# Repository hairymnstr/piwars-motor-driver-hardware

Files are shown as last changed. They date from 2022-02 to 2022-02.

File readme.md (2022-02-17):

# Motor and Servo Driver Board

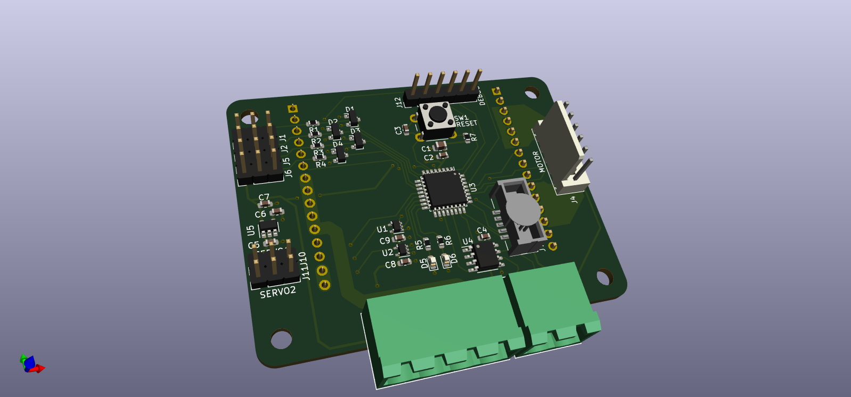
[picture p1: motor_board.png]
Motor and Servo control board


This small board was designed for our robot in PiWars 2021.
It's designed to drive a small DC motor up to ~4A/12V with optional quadrature encoder feedback and up to two servo motors.
The board interfaces with a host system via RS485 and its address is set with three jumpers on the board, so you can have up to 8 of these on a single 485 bus.
In the competition we used 6 of these, four for our all-wheel steering robot and two for a grab arm.  In total we used 6 servos and 6 DC motors.  All were controlled via a RaspberryPi with negligible lag.

The actual H-bridge in this module is an ST VNH7070AS mounted on an eval board. <https://uk.farnell.com/stmicroelectronics/ev-vnh7070as/eval-board-high-bridge-motor-driver>  I chose the eval board option because the part had a thermal slug underneath it and I didn't have a way to surface mount it at home.

## Issues

There are a couple of issues with the current board:

1. The servo connector pinout is wrong for all standard servos.  When I designed the board I didn't think to check and placed the signal in the middle pin between the power and ground.  RC servos are normally Gnd-Pwr-Sig.  You can work around this by carefully removing the signal and power wires from the connector shell and re-inserting them in the special order required.

2. There should be a bulk capacitor on the 5V rail.  Our robot had a big (3A) 5V regulator which powered all the control electronics so these boards were designed to use that as the power for their logic (via a 3.3V low input regulator) and the servos.  Using MG996R servos I kept "popping" the 3.3V regulator.  The fix was to add a bulk capacitance locally to smooth out the spikes caused by the servo.  In my current design I'm also coupling each board with an LM2596 DC-DC regulator to generate 6V for the servos and feed the 3.3V regulator so the whole assembly only needs a wide-range raw battery voltage input.

## Firmware

Firmware is in another repository and currently only supports one motor without encoder and a single servo.  See <https://github.com/hairymnstr/piwars-motor-driver-firmware>.

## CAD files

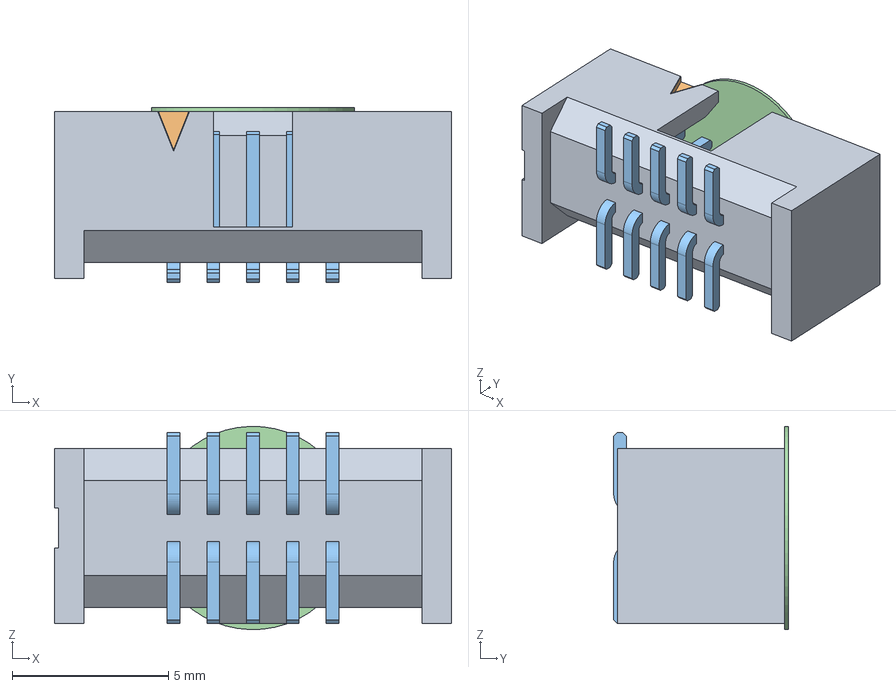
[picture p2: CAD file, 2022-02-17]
SHF-105-01-L-D-SM-K-TR.stp
12.7 x 5.59 x 6.50 mm
_SHF-105-01-D_header
_SHF-First_Position_Indicator
_T-1S71-02-05-D-SM
_K-DOT-0.256-0.375-0.005_polyamide_pick_

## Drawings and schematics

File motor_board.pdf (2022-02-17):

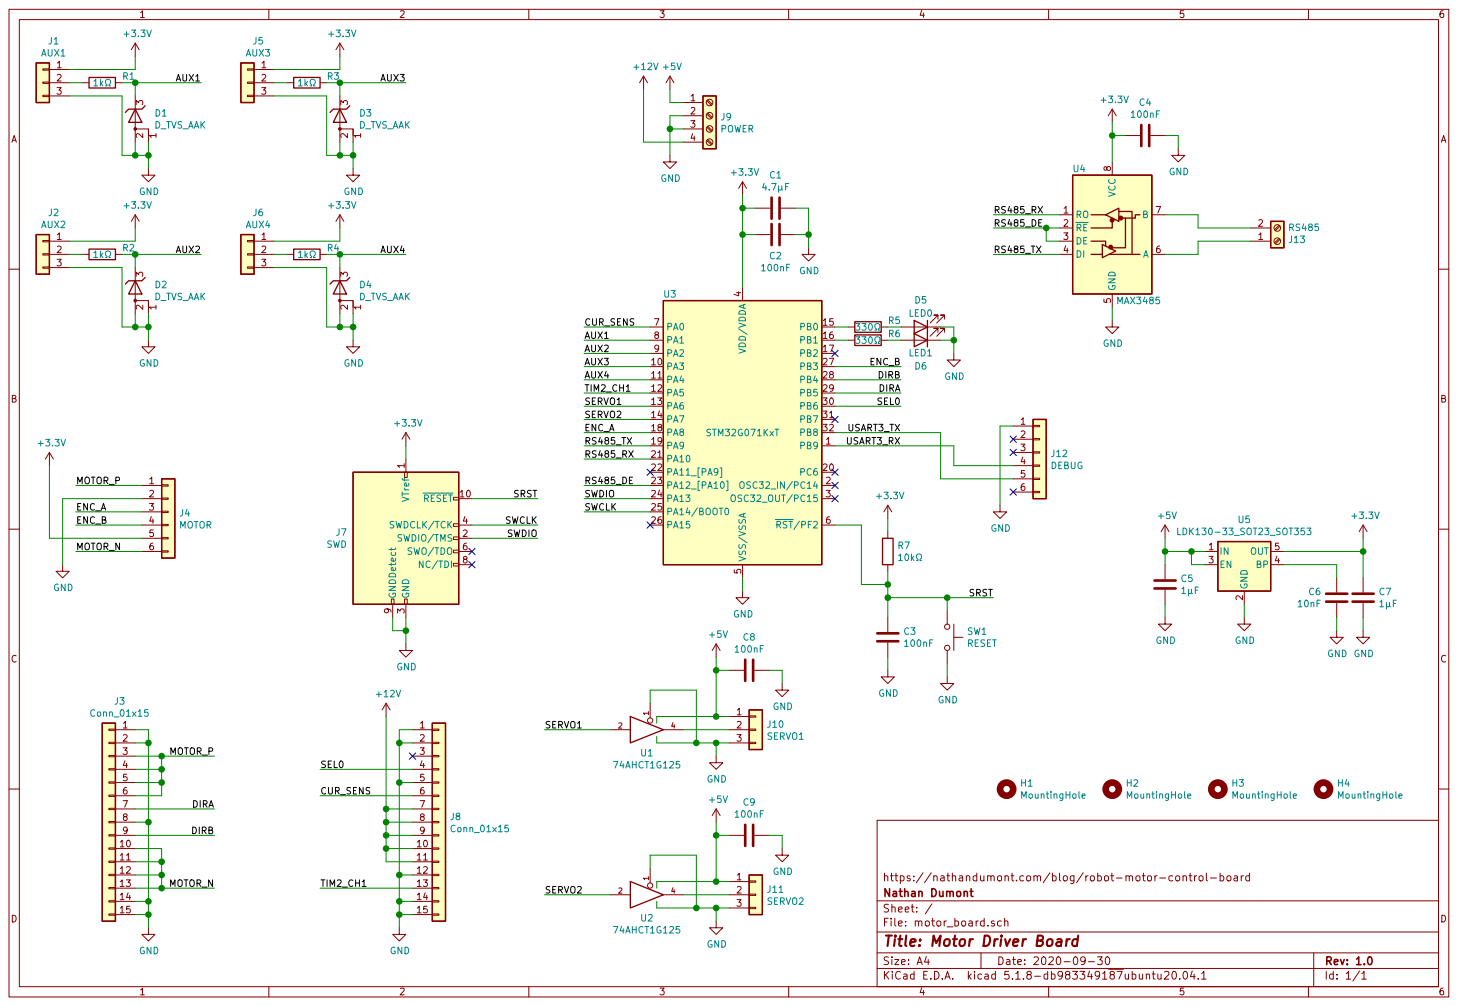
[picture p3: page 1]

3 SWDCLK/TCK 4 SWO/TDO 6 NC/TDI 8 GNDDetect 9

File: motor_board.sch Sheet: / Nathan Dumont https://nathandumont.com/blog/robot-motor-control-board

Id: 1/1 Title: Motor Driver Board

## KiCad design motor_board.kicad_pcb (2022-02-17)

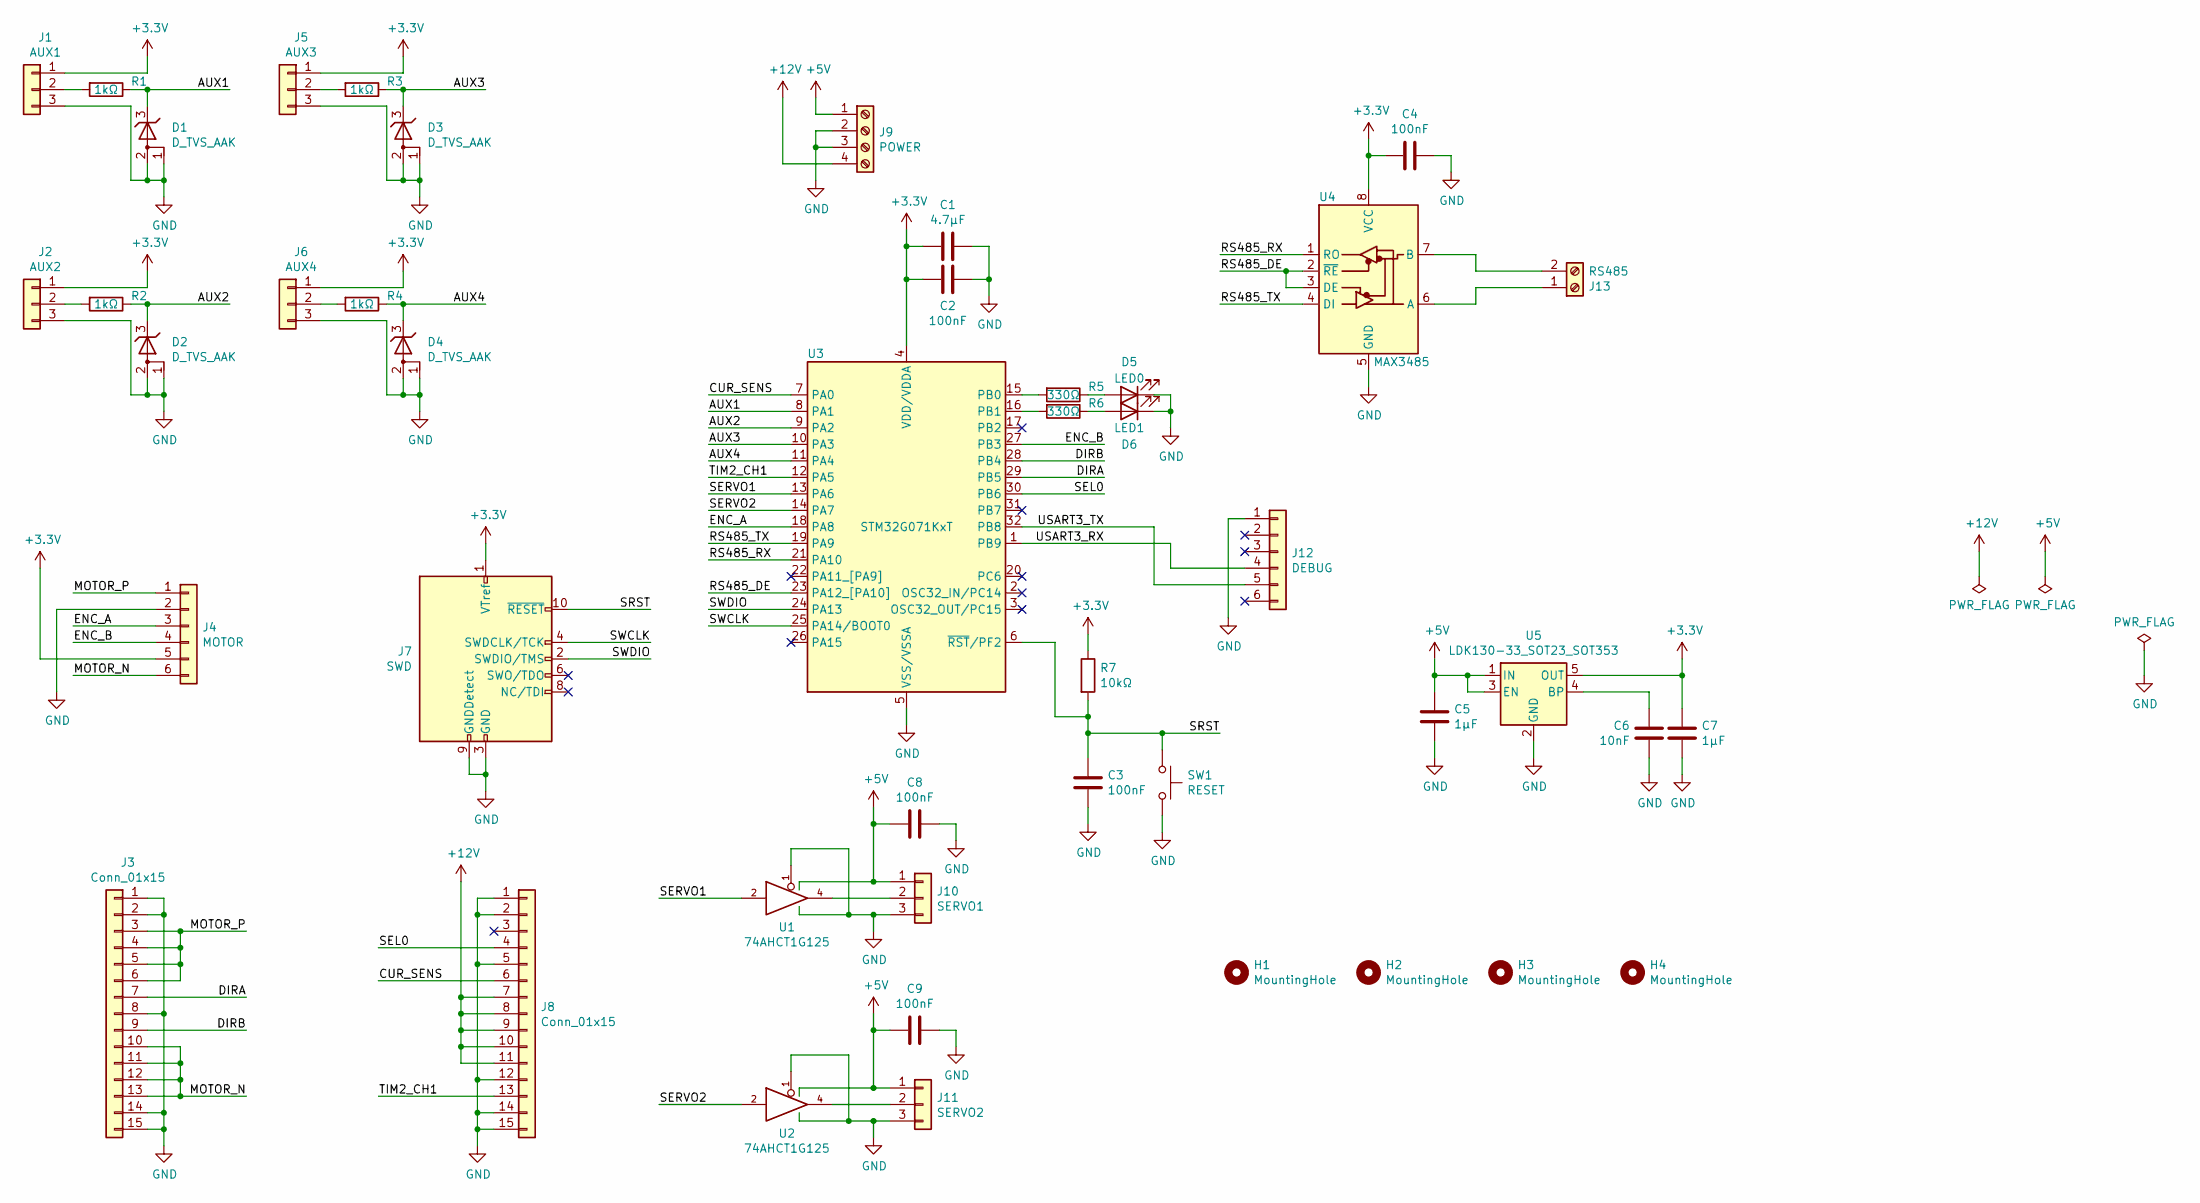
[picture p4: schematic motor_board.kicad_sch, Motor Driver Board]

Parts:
C1: 4.7µF; C_0805_2012Metric
C2, C3, C4, C8, C9: 100nF; C_0603_1608Metric
C5, C7: 1µF; C_0603_1608Metric
C6: 10nF; C_0603_1608Metric
D1, D2, D3, D4: D_TVS_AAK; SOT-23; Part number BOURNS CDSOT23-T03-Q; Farnell 3015164
D5: LED0; LED_0603_1608Metric; Part number KINGBRIGHT KPT-1608EC; Farnell 2099221
D6: LED1; LED_0603_1608Metric; Part number KINGBRIGHT KPH-1608SGC; Farnell 2426215
H1, H2, H3, H4: MountingHole; MountingHole_3.2mm_M3
J1: AUX1; PinHeader_1x03_P2.54mm_Vertical
J2: AUX2; PinHeader_1x03_P2.54mm_Vertical
J3: Conn_01x15; PinHeader_1x15_P2.54mm_Vertical
J4: MOTOR; Molex_KK-254_AE-6410-06A_1x06_P2.54mm_Vertical; Part number MOLEX 22-27-2061; Farnell 9731172
J5: AUX3; PinHeader_1x03_P2.54mm_Vertical
J6: AUX4; PinHeader_1x03_P2.54mm_Vertical
J7: SWD; SAMTEC_SHF-SM_5x2
J8: Conn_01x15; PinSocket_1x15_P2.54mm_Vertical
J9: POWER; PhoenixContact_MSTBA_2,5_4-G-5,08_1x04_P5.08mm_Horizontal; Part number PHOENIX CONTACT MSTBA 2,5/ 4-G-5,08; Farnell 3705195
J10: SERVO1; PinHeader_1x03_P2.54mm_Vertical
J11: SERVO2; PinHeader_1x03_P2.54mm_Vertical
J12: DEBUG; PinHeader_1x06_P2.54mm_Vertical
J13: RS485; PhoenixContact_MSTBA_2,5_2-G-5,08_1x02_P5.08mm_Horizontal; Part number PHOENIX CONTACT MSTBA 2,5/ 2-G-5,08; Farnell 3705171
R1, R2, R3, R4: 1kΩ; R_0603_1608Metric
R5, R6: 330Ω; R_0603_1608Metric; Part number MULTICOMP MCWR06X3300FTL; Farnell 2447339
R7: 10kΩ; R_0603_1608Metric
SW1: RESET; SW_PUSH_6mm
U1, U2: 74AHCT1G125; SOT-353_SC-70-5; Part number TI SN74AHCT1G125DCKR; Farnell 3006131
U3: STM32G071KxT; LQFP-32_7x7mm_P0.8mm; Part number ST STM32G071KBT6; Farnell 2980897
U4: MAX3485; SOIC-8_3.9x4.9mm_P1.27mm; Part number MAXIM MAX3485CSA+; Farnell 2512100
U5: LDK130-33_SOT23_SOT353; SOT-23-5; Part number ST LDK130M33R; Farnell 2849788

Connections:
+3V3: C1.2, C2.2, C4.2, C7.1, J1.1, J2.1, J4.5, J5.1, J6.1, J7.1 (VTref), R7.1, U3.4 (VDD/VDDA), U4.8 (VCC), U5.5 (OUT)
+5V: C5.1, C8.2, C9.2, J9.1, J10.1, J11.1, U1.5 (VCC), U2.5 (VCC), U5.1 (IN), U5.3 (EN)
+12V: J8.7, J8.8, J8.9, J8.10, J8.11, J9.4
/AUX1: D1.3 (K), R1.1, U3.8 (PA1)
/AUX2: D2.3 (K), R2.1, U3.9 (PA2)
/AUX3: D3.3 (K), R3.1, U3.10 (PA3)
/AUX4: D4.3 (K), R4.1, U3.11 (PA4)
/CUR_SENS: J8.6, U3.7 (PA0)
/DIRA: J3.7, U3.29 (PB5)
/DIRB: J3.9, U3.28 (PB4)
/ENC_A: J4.3, U3.18 (PA8)
/ENC_B: J4.4, U3.27 (PB3)
/MOTOR_N: J3.10, J3.11, J3.12, J3.13, J4.6
/MOTOR_P: J3.3, J3.4, J3.5, J3.6, J4.1
/RS485_DE: U3.23 (PA12_[PA10]), U4.2 (~RE), U4.3 (DE)
/RS485_RX: U3.21 (PA10), U4.1 (RO)
/RS485_TX: U3.19 (PA9), U4.4 (DI)
/SEL0: J8.4, U3.30 (PB6)
/SERVO1: U1.2, U3.13 (PA6)
/SERVO2: U2.2, U3.14 (PA7)
/SRST: C3.1, J7.10 (~RESET), R7.2, SW1.1, U3.6 (~RST/PF2)
/SWCLK: J7.4 (SWDCLK/TCK), U3.25 (PA14/BOOT0)
/SWDIO: J7.2 (SWDIO/TMS), U3.24 (PA13)
/TIM2_CH1: J8.13, U3.12 (PA5)
/USART3_RX: J12.4, U3.1 (PB9)
/USART3_TX: J12.5, U3.32 (PB8)
GND: C1.1, C2.1, C3.2, C4.1, C5.2, C6.2, C7.2, C8.1, C9.1, D1.1 (A), D1.2 (A), D2.1 (A), D2.2 (A), D3.1 (A), D3.2 (A), D4.1 (A), D4.2 (A), D5.1 (K), D6.1 (K), J1.3, J2.3, J3.1, J3.2, J3.8, J3.14, J3.15, J4.2, J5.3, J6.3, J7.3 (GND), J7.5 (GND), J7.9 (GNDDetect), J8.1, J8.2, J8.5, J8.12, J8.14, J8.15, J9.2, J9.3, J10.3, J11.3, J12.1, SW1.2, U1.1, U1.3 (GND), U2.1, U2.3 (GND), U3.5 (VSS/VSSA), U4.5 (GND), U5.2 (GND)
unnamed: C6.1, U5.4 (BP)
unnamed: D5.2 (A), R5.1
unnamed: D6.2 (A), R6.1
unnamed: J1.2, R1.2
unnamed: J2.2, R2.2
unnamed: J5.2, R3.2
unnamed: J6.2, R4.2
unnamed: J10.2, U1.4
unnamed: J11.2, U2.4
unnamed: J13.1, U4.6 (A)
unnamed: J13.2, U4.7 (B)
unnamed: R5.2, U3.15 (PB0)
unnamed: R6.2, U3.16 (PB1)

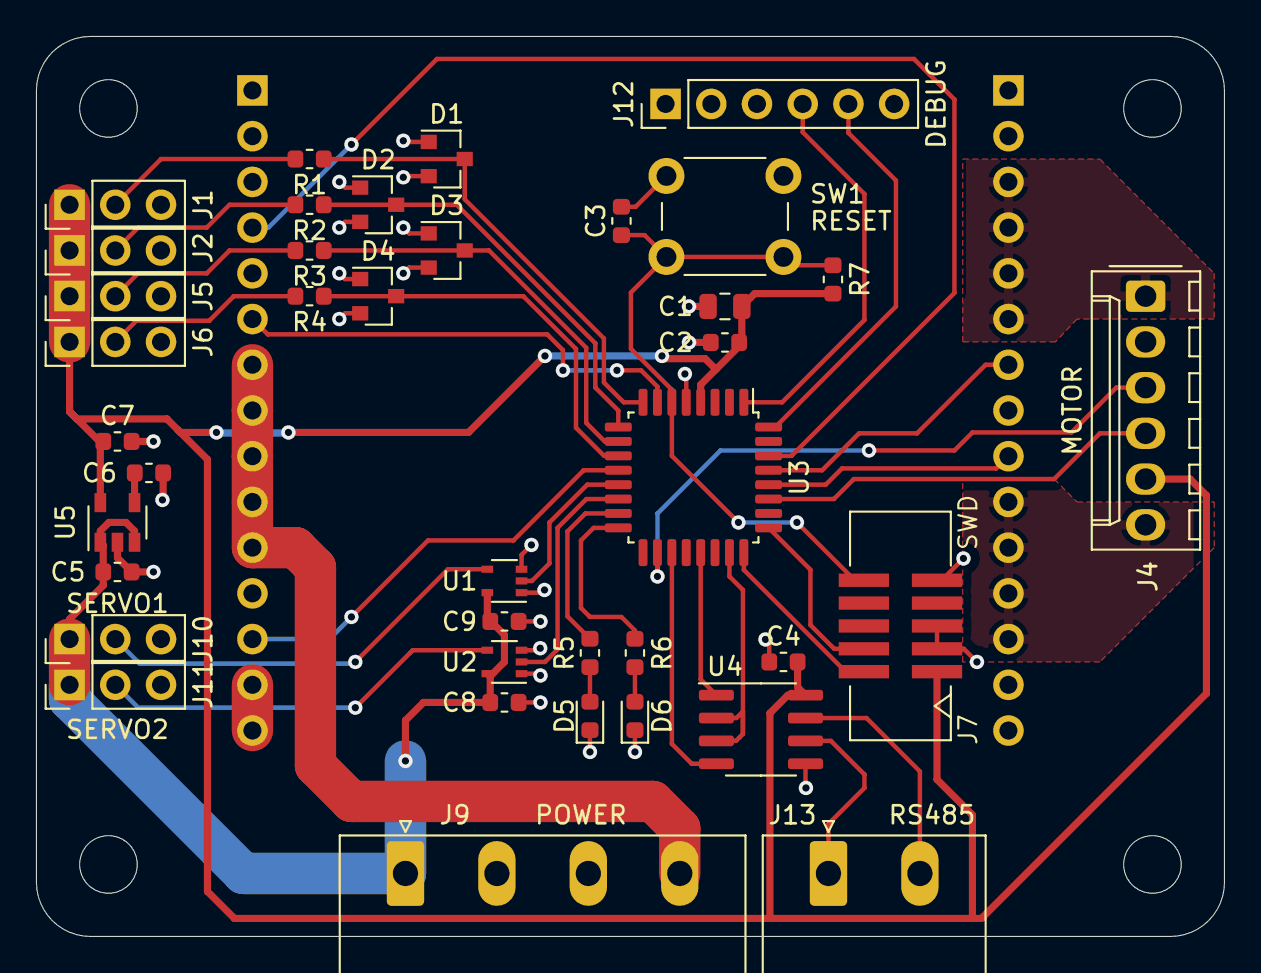
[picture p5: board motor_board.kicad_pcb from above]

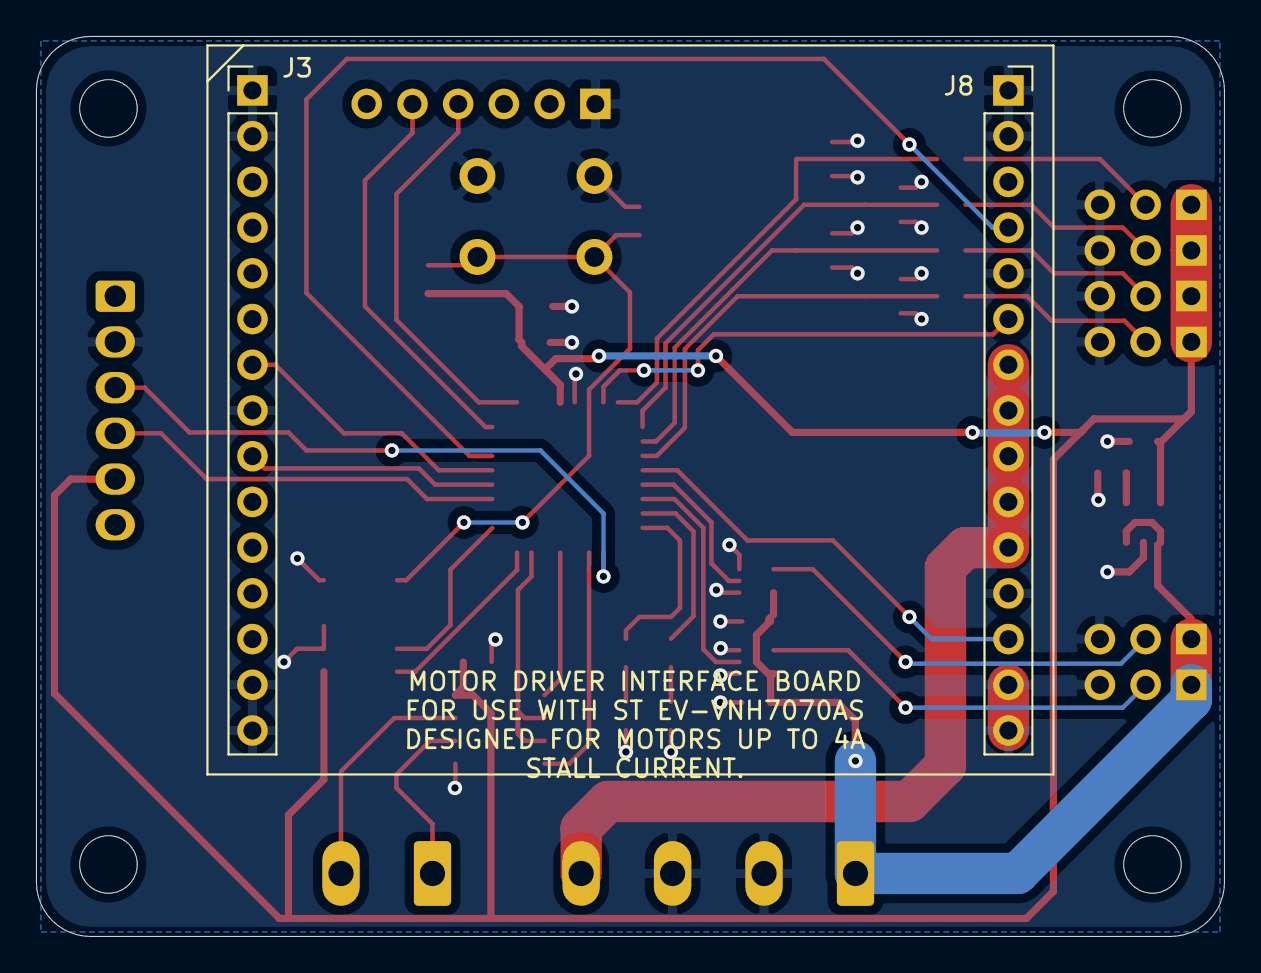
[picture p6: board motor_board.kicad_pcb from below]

Board: 2 copper layers, 66.0 x 50.0 mm, 45 parts (2 on the bottom side), 40 nets.

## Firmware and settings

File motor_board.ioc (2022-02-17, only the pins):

Mcu.UserName=STM32G071KBTx
PB0.GPIO_Label=LED0
PB6.GPIO_Label=SEL0
PB6.Signal=GPIO_Output
PA14-BOOT0.Signal=SYS_SWCLK
PB1.GPIO_Label=LED1
PA8.Signal=S_TIM1_CH1
PA0.Signal=ADC1_IN0
PB9.Signal=USART3_RX
PB1.Signal=GPIO_Output
PA6.Signal=S_TIM3_CH1
PA10.Signal=USART1_RX
PB5.GPIO_Label=DIRB
PB4.Signal=GPIO_Output
PA3.Signal=ADC1_IN3
PA13.Signal=SYS_SWDIO
PA9.Signal=USART1_TX
PA1.Signal=ADC1_IN1
PA5.Signal=S_TIM2_CH1
PB4.GPIO_Label=DIRA
PA2.Signal=ADC1_IN2
PB3.Signal=S_TIM1_CH2
PA4.Signal=ADC1_IN4
PB5.Signal=GPIO_Output
PB8.Signal=USART3_TX
PB0.Signal=GPIO_Output
PA7.Signal=S_TIM3_CH2

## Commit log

2022-02-17 Finally preparing to push to github
    [SHF-105-01-L-D-SM-K-TR.stp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]
2022-02-17 Updated to KiCad 6
    [motor_board.kicad_pcb, motor_board.kicad_sch]
2022-02-17 Excluded the new KiCad 6 backups folder

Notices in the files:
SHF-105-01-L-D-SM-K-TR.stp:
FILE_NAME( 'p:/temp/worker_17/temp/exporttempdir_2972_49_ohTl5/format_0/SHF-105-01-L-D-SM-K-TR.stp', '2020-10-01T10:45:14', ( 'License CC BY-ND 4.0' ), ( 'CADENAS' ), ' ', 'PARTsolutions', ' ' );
